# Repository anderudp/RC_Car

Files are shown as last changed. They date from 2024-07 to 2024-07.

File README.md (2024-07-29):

# ESP32 remote controlled toy car
This is a simple RC car library which uses Expressif's ESP-NOW for wireless control. Written in C++ using PlatformIO with the Arduino framework in VS Code.

## Bill of materials
 - 2 x ESP32 dev boards (Tested on HW-394 boards)
 - 1 x 5-pin joystick module
 - 2 x L298N H-bridge dual motor driver module
 - 4 x generic DC motor + wheels (Tested with d=65mm ones)
 - Chassis compatible with the motors
 - 2 x power source (USB power bank, 9v battery, etc.)
 - Jumper wires

## Physical build
### Car body
Mount the motors to the chassis according to the manufacturer's instructions. Afterwards wire in the components as follows:

car body wiring diagram

Make sure to bridge the 5VEN pins on the motor drivers (indicated by yellow wires).

### Remote controller
Connect the joystick to the ESP32.

joystick controller wiring diagram

You may want to build a chassis for the remote for ease of use. I suggest getting creative with it. 🙂

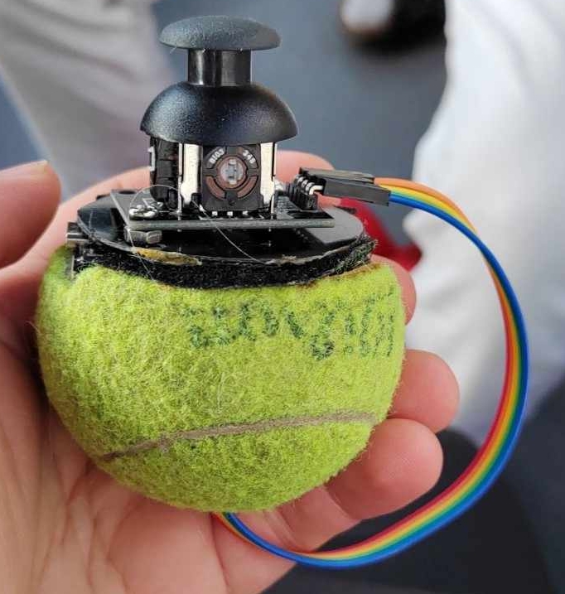
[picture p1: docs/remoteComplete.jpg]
remote controller tennis ball


## Programming the ESPs
You will need your car ESP's MAC address for communication. The simplest way to check it is to upload the following program to it and opening a serial monitor on the appropriate terminal. Make sure to configure the monitor's baud rate to 115200.

```c++
#include <Arduino.h>
#include <WiFi.h>
void setup()
{
    Serial.begin(115200);
    WiFi.mode(WIFI_STA);
}
void loop()
{
    Serial.println(WiFi.macAddress());
}
```
Once you have the MAC address, head to `joyControl/src/main.cpp` and replace the byte hexes in `broadcastAddress[]` with those of your ESP's MAC address.

Using the PlatformIO extension in VS Code, build and upload `joyControl` to the remote controller's ESP, and `carBody` to the car ESP. On Linux, you must enable the connecting USB terminal:
```bash
sudo chmod a+rw /dev/ttyUSB0
```
Your ESP might be connected on a different terminal. Check if the PlatformIO extension can detect the port your ESP board is connected on. If none are found, try restarting your computer, and if it still does not show up, try a different USB cable.

## Operation
The remote controller reads the values of the joystick. This is comprised of the readings of two perpendicularly aligned potentiometers and that of a button (here used for braking). The values of the pots form a square, with additional dead space in the circumircle.

The remote controller converts these readings into polar notation, with the distance `r` from the joystick's center being calculated as the maximum of the two coordinates (Chebyshev distance), and the direction `theta` calculated using 2-argument arctangent, resulting in the following radian representation:

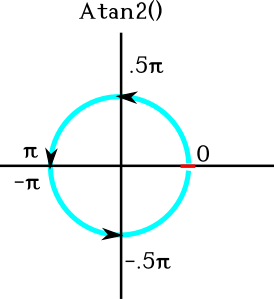
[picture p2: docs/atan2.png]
atan2 directions in radians


The car's microcontroller receives these values, and performs skid steering. The speed of the motors on each side is calculated by multiplying `r` by the following coefficient function based on `theta`:

skid steering functions

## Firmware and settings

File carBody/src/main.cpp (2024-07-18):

#include <Arduino.h>
#include <WiFi.h>
#include <esp_now.h>

#define REAR_ENA 25
#define REAR_R_IN1 26
#define REAR_R_IN2 27
#define REAR_L_IN3 14
#define REAR_L_IN4 12
#define REAR_ENB 13

#define FRONT_ENA 15
#define FRONT_R_IN1 2
#define FRONT_R_IN2 4
#define FRONT_L_IN3 16
#define FRONT_L_IN4 17
#define FRONT_ENB 5

#define HALF_PI 1.57079632679

typedef struct remoteMsg {
    unsigned int count;
    unsigned char r;
    float theta;
    bool btn;
} remoteMsg;

remoteMsg controlSignal;

unsigned char wheelPins[8] = {REAR_R_IN1, REAR_R_IN2, REAR_L_IN3, REAR_L_IN4, FRONT_R_IN1, FRONT_R_IN2, FRONT_L_IN3, FRONT_L_IN4}; 
unsigned char wheelEnables[4] = {REAR_ENA, REAR_ENB, FRONT_ENA, FRONT_ENB};

/**
 * @brief  Sets one of the wheels to a desired speed.
 * 
 * @param  whl:  Wheel to control. Range: [0, 3]. (0)RearR, (1)RearL, (2)FrontR, (3)FrontL
 * @param  spd:  Ratio of maximum motor output in either direction. Range: [-255, 255].
 */
void setWheel(unsigned char whl, int spd)
{
    bool fwd = spd > 0;
    digitalWrite(wheelPins[2 * whl], fwd ? HIGH : LOW);
    digitalWrite(wheelPins[2 *  whl + 1], fwd ? LOW : HIGH);
    analogWrite(wheelEnables[whl], abs(spd));
}

void brake()
{
    for (unsigned char in : wheelPins)
    {
        digitalWrite(in, LOW);
    }
    for (unsigned char en : wheelEnables)
    {
        analogWrite(en, 255);
    }
}

float leftPwmCoeff(float angle)
{
    if(angle <= -HALF_PI) return -1;
    else if(angle <= 0) return cos(2 * angle);
    else if(angle <= HALF_PI) return 1;
    else return sin(2 * angle - HALF_PI);
}

float rightPwmCoeff(float angle)
{
    if(angle <= -HALF_PI) return cos(2 * angle);
    else if(angle <= 0) return -1;
    else if(angle <= HALF_PI) return sin(2 * angle - HALF_PI);
    else return 1;
}

void OnDataRecv(const uint8_t *mac, const uint8_t *incomingData, int len) 
{
    memcpy(&controlSignal, incomingData, sizeof(controlSignal));
    Serial.print(controlSignal.count); Serial.print(",");
    Serial.print(controlSignal.btn); Serial.print(",");
    if(controlSignal.r < 30)
    {
        controlSignal.r = 0;
    }
    if(controlSignal.btn)
    {
        brake();
        Serial.println("0,0");
    }
    else
    {
        int leftPWM = ceil(controlSignal.r * leftPwmCoeff(controlSignal.theta));
        int rightPWM = ceil(controlSignal.r * rightPwmCoeff(controlSignal.theta));
        Serial.print(leftPWM); Serial.print(","); Serial.println(rightPWM);
        setWheel(0, rightPWM); setWheel(2, rightPWM);
        setWheel(1, leftPWM); setWheel(3, leftPWM);
    }
}

void setup() 
{
    Serial.begin(115200);
    WiFi.mode(WIFI_STA);
    if (esp_now_init() != ESP_OK) return;
    pinMode(REAR_ENA, OUTPUT);
    pinMode(REAR_R_IN1, OUTPUT);
    pinMode(REAR_R_IN2, OUTPUT);
    pinMode(REAR_L_IN3, OUTPUT);
    pinMode(REAR_L_IN4, OUTPUT);
    pinMode(REAR_ENB, OUTPUT);

    pinMode(FRONT_ENA, OUTPUT);
    pinMode(FRONT_R_IN1, OUTPUT);
    pinMode(FRONT_R_IN2, OUTPUT);
    pinMode(FRONT_L_IN3, OUTPUT);
    pinMode(FRONT_L_IN4, OUTPUT);
    pinMode(FRONT_ENB, OUTPUT);

    digitalWrite(REAR_R_IN1, LOW);
    digitalWrite(REAR_R_IN2, LOW);
    digitalWrite(REAR_L_IN3, LOW);
    digitalWrite(REAR_L_IN4, LOW);
    analogWrite(REAR_ENA, 0);
    analogWrite(REAR_ENB, 0);

    digitalWrite(FRONT_R_IN1, LOW);
    digitalWrite(FRONT_R_IN2, LOW);
    digitalWrite(FRONT_L_IN3, LOW);
    digitalWrite(FRONT_L_IN4, LOW);
    analogWrite(FRONT_ENA, 0);
    analogWrite(FRONT_ENB, 0);

    esp_now_register_recv_cb(OnDataRecv);
}

void loop()
{
    
}

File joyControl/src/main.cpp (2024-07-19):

#include <Arduino.h>
#include "WiFi.h"
#include <esp_now.h>

#define VRx 33
#define VRy 32
#define SW 13
#define LED 2

uint8_t broadcastAddress[] = {0xA0, 0xDD, 0x6C, 0x03, 0x03, 0x90};

unsigned int counter = 0;

typedef struct remoteMsg {
    unsigned int count;
    unsigned char r;
    float theta;
    bool btn;
} remoteMsg;

remoteMsg controlSignal;

esp_now_peer_info_t peerInfo;

void OnDataSent(const uint8_t *mac, esp_now_send_status_t status) 
{
    if(status == ESP_NOW_SEND_SUCCESS)
    {
        Serial.println(",0");
        analogWrite(LED, 127);
        delay(10);
        analogWrite(LED, 0);
    }
    else
    {
        Serial.println(",1");
    }
}

void setup()
{
    Serial.begin(115200);
    pinMode(VRx, INPUT);
    pinMode(VRy, INPUT);
    pinMode(SW, INPUT_PULLUP);
    pinMode(LED, OUTPUT);
    adcAttachPin(VRx);
    adcAttachPin(VRy);

    WiFi.mode(WIFI_STA);
    if (esp_now_init() != ESP_OK) return;
    esp_now_register_send_cb(OnDataSent);

    memcpy(peerInfo.peer_addr, broadcastAddress, 6);
    peerInfo.channel = 0;  
    peerInfo.encrypt = false;
    if (esp_now_add_peer(&peerInfo) != ESP_OK) return;

    counter = 0;
}

void loop()
{
    controlSignal.count = counter;

    bool sw = 1 - digitalRead(SW);
    controlSignal.btn = sw;

    int x = map(analogRead(VRx), 0, 4095, -255, 255);
    int y = map(analogRead(VRy), 0, 4095, -255, 255);
    // Chebyshev distance
    unsigned char r = max(abs(x), abs(y));
    controlSignal.r = r;

    float theta = atan2(x, y);
    controlSignal.theta = theta;

    Serial.print(counter++); Serial.print(",");
    Serial.print(sw ? 1 : 0); Serial.print(",");
    Serial.print(r); Serial.print(",");
    Serial.print(theta);

    esp_err_t result = esp_now_send(broadcastAddress, (uint8_t *) &controlSignal, sizeof(controlSignal));
    delay(100);
}

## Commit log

2024-07-18 speeds are now applied to motors
2024-07-20 created unified readme file, collected docs
    [carBody.fzz, joyControl.fzz]
